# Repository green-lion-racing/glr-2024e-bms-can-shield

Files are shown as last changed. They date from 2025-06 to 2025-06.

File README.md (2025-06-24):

# CAN-Shield for NUCLEO-G474RE

NUCLEO-G474RE compatible CAN shield, which is our main microcontroller for the battery management system (BMS/AMS).

### Overview

Acts as can transciever for the BMS. 
Has two 12V output pins, one in case of a BMS fault. The other to set the state (on/off) of the HV charger.

CAN 1 is designated for the communication with FSGs datalogger, because of the high 1Mbit CAN baudrate.

CAN 2 is designated to communicate with the rest of the car, at a lower baudrate.

Compatible to the Analog Devices EVAL-ADBMS6822 board, can be directly slotted onto the nucleo board at the same time.

WR-TBL 3.5mm Connectors for signals to and from the board.

### Used parts

> [!WARNING]  
> Part list is not complete.

| Article | Description | Link | Quantity |
| --- | --- | --- | --- |
| Infineon TLE6250GV33XUMA1 | can transiever | https://www.mouser.de/ProductDetail/Infineon-Technologies/TLE6250GV33XUMA1?qs=OwbwYO03UsJ9UcCPEQ3lNA%3D%3D | 2 |
| Omron G5V-2-DC12 | relais | https://www.mouser.de/ProductDetail/Omron-Electronics/G5V-2-DC12?qs=lK7M36XCk6JxdWY%2FV6sVqw%3D%3D | 1 |
| STMicroelectronics ESDCAN01-2BLY | dual-line TVS diode | https://www.mouser.de/ProductDetail/STMicroelectronics/ESDCAN01-2BLY?qs=Ok1pvOkw6%2FpNzC2RQnWwPA%3D%3D | 2 |
| | transistor | | |
| Samsung CL10B104KB8NNNC | capacitor 100nF | https://www.mouser.de/ProductDetail/Samsung-Electro-Mechanics/CL10B104KB8NNNC?qs=349EhDEZ59rvGc2rLwVOdA%3D%3D | 2 |
| Vishay CRCW060368R1FKEA | resistor 68ohm | https://www.mouser.de/ProductDetail/Vishay-Dale/CRCW060368R1FKEA?qs=6z8JnUK2jyMngsBXu5il1A%3D%3D | 4 |
| Samtec SSW-119-01-T-D-LL | 02x19  Mounting Pin, 2.54 mm | https://www.mouser.de/ProductDetail/Samtec/SSW-119-01-T-D-LL?qs=F1JzWfReSMQC5N%252BZEM9ULw%3D%3D | 2 |
| Würth Elektronik 691321100002 | 2-pin header | https://www.mouser.de/ProductDetail/Wurth-Elektronik/691321100002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 | 1 |
| Würth Elektronik 691361100002 | 2-pin plug | https://www.mouser.de/ProductDetail/Wurth-Elektronik/691361100002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 | 1 |
| Würth Elektronik 691321100004 | 4-pin header | https://www.mouser.de/ProductDetail/Wurth-Elektronik/691321100004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 | 2 |
| Würth Elektronik 691361100004 | 4-pin plug | https://www.mouser.de/ProductDetail/Wurth-Elektronik/691361100004?qs=2kOmHSv6VfRmrzXJBP%2F4Sg%3D%3D | 2 |

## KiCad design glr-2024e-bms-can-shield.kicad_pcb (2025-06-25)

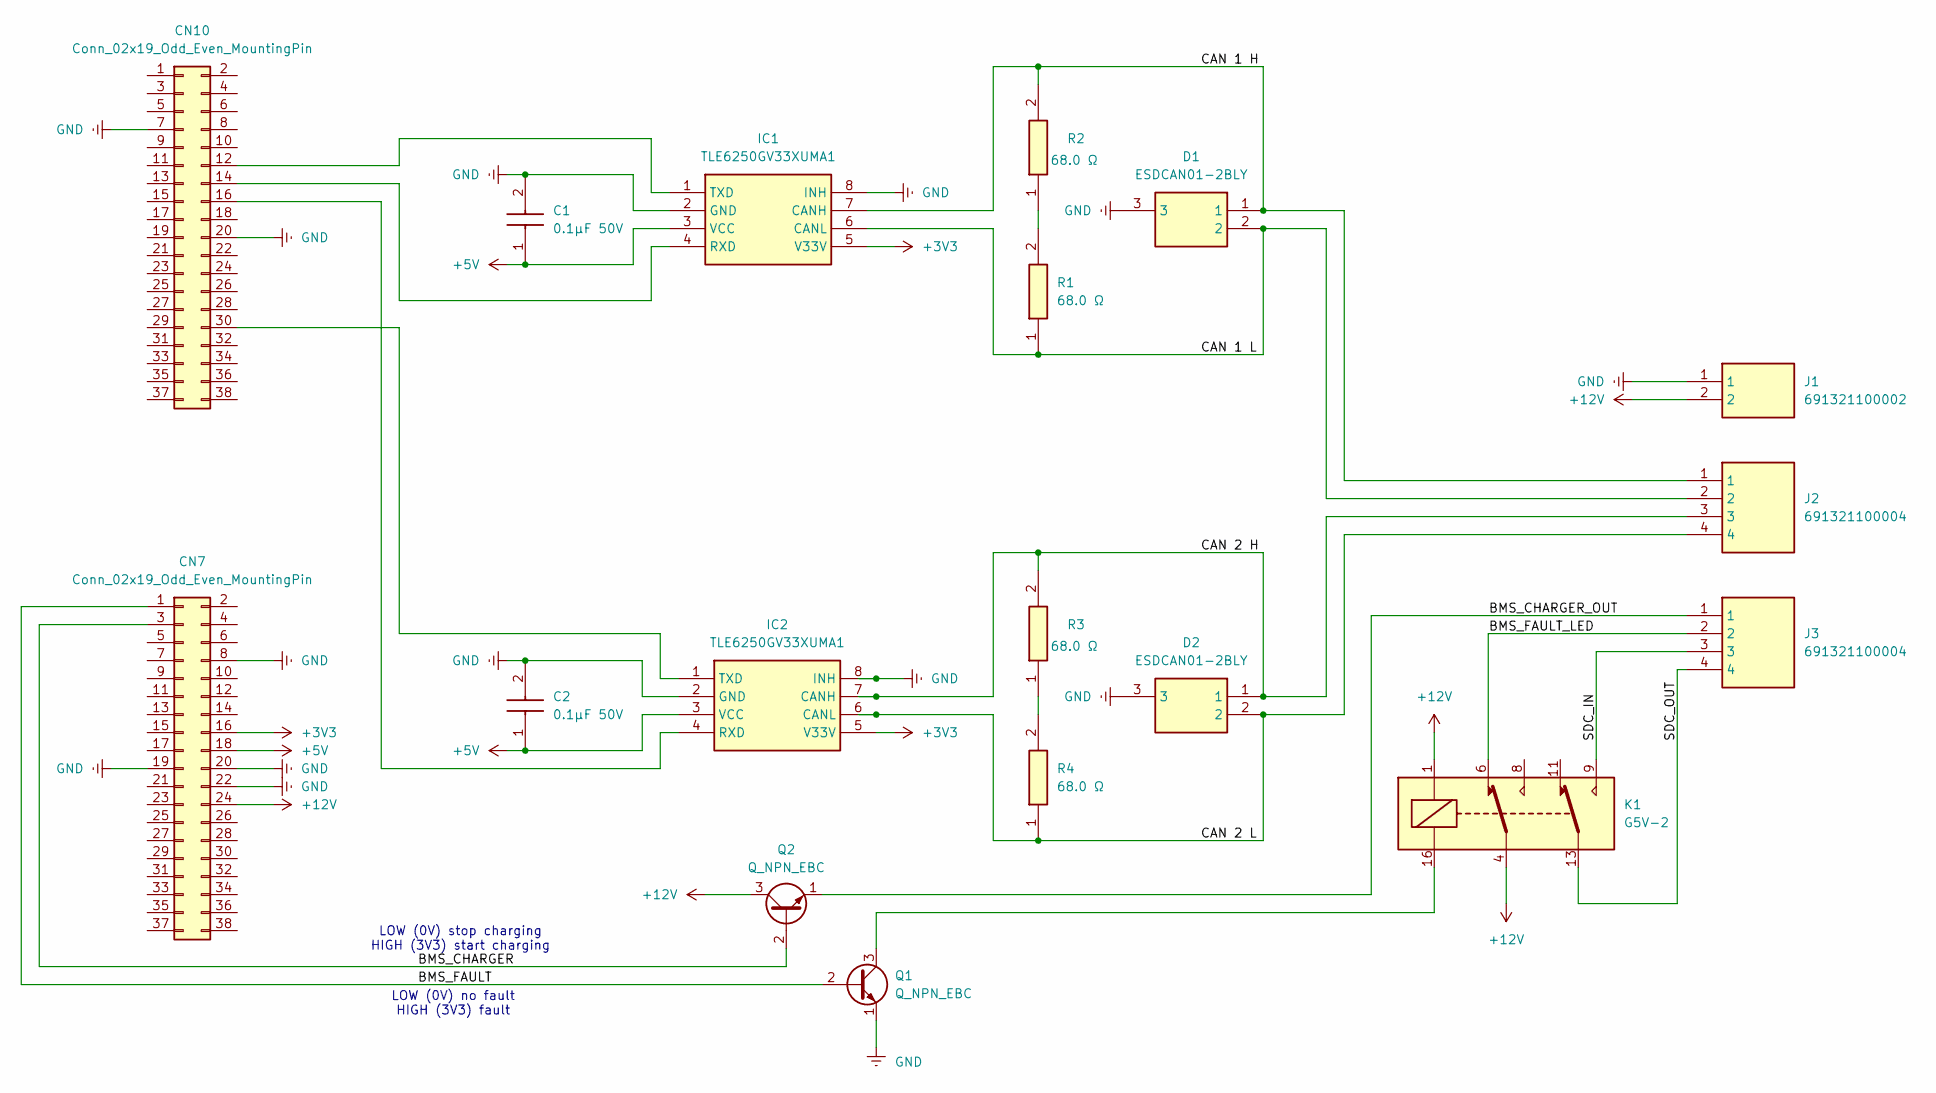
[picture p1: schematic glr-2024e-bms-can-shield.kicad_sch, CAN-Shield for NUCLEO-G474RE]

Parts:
C1, C2: 0.1μF 50V; CAPC1608X90N; Manufacturer_Part_Number CL10B104KB8NNNC
CN7, CN10: Conn_02x19_Odd_Even_MountingPin; PinSocket_2x19_P2.54mm_Vertical
D1, D2: ESDCAN01-2BLY; SOT95P255X125-3N; Mouser Part Number 511-ESDCAN01-2BLY
IC1, IC2: TLE6250GV33XUMA1; SOIC127P600X175-8N; Mouser Part Number 726-TLE6250GV33XUMA1
J1: 691321100002; Mouser Part Number 710-691321100002
J2, J3: 691321100004; Mouser Part Number 710-691321100004
K1: G5V-2; Relay_DPDT_Omron_G5V-2
Q1: Q_NPN_EBC; TO-18-3
Q2: Q_NPN_EBC; SOT-23
R1, R2, R3, R4: 68.0 Ω; RESC1608X50N; Manufacturer_Part_Number CRCW060368R1FKEA

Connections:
+3V3: CN7.16, IC1.5 (V33V), IC2.5 (V33V)
+5V: C1.1, C2.1, CN7.18, IC1.3 (VCC), IC2.3 (VCC)
+12V: CN7.24, J1.2, K1.1, K1.4, Q2.3 (C)
/BMS_CHARGER: CN7.3, Q2.2 (B)
/BMS_CHARGER_OUT: J3.1, Q2.1 (E)
/BMS_FAULT: CN7.1, Q1.2 (B)
/BMS_FAULT_LED: J3.2, K1.6
/CAN 1 H: D1.1, IC1.7 (CANH), J2.1, R2.2
/CAN 1 L: D1.2, IC1.6 (CANL), J2.2, R1.1
/CAN 2 H: D2.1, IC2.7 (CANH), J2.3, R3.2
/CAN 2 L: D2.2, IC2.6 (CANL), J2.4, R4.1
/SDC_IN: J3.3, K1.9
/SDC_OUT: J3.4, K1.13
GND: C1.2, C2.2, CN7.8, CN7.19, CN7.20, CN7.22, CN10.7, CN10.20, D1.3, D2.3, IC1.2 (GND), IC1.8 (INH), IC2.2 (GND), IC2.8 (INH), J1.1, Q1.1 (E)
unnamed: CN10.12, IC1.1 (TXD)
unnamed: CN10.14, IC1.4 (RXD)
unnamed: CN10.16, IC2.4 (RXD)
unnamed: CN10.30, IC2.1 (TXD)
unnamed: K1.16, Q1.3 (C)
unnamed: R1.2, R2.1
unnamed: R3.1, R4.2

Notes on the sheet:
LOW (0V) stop charging HIGH (3V3) start charging
LOW (0V) no fault HIGH (3V3) fault

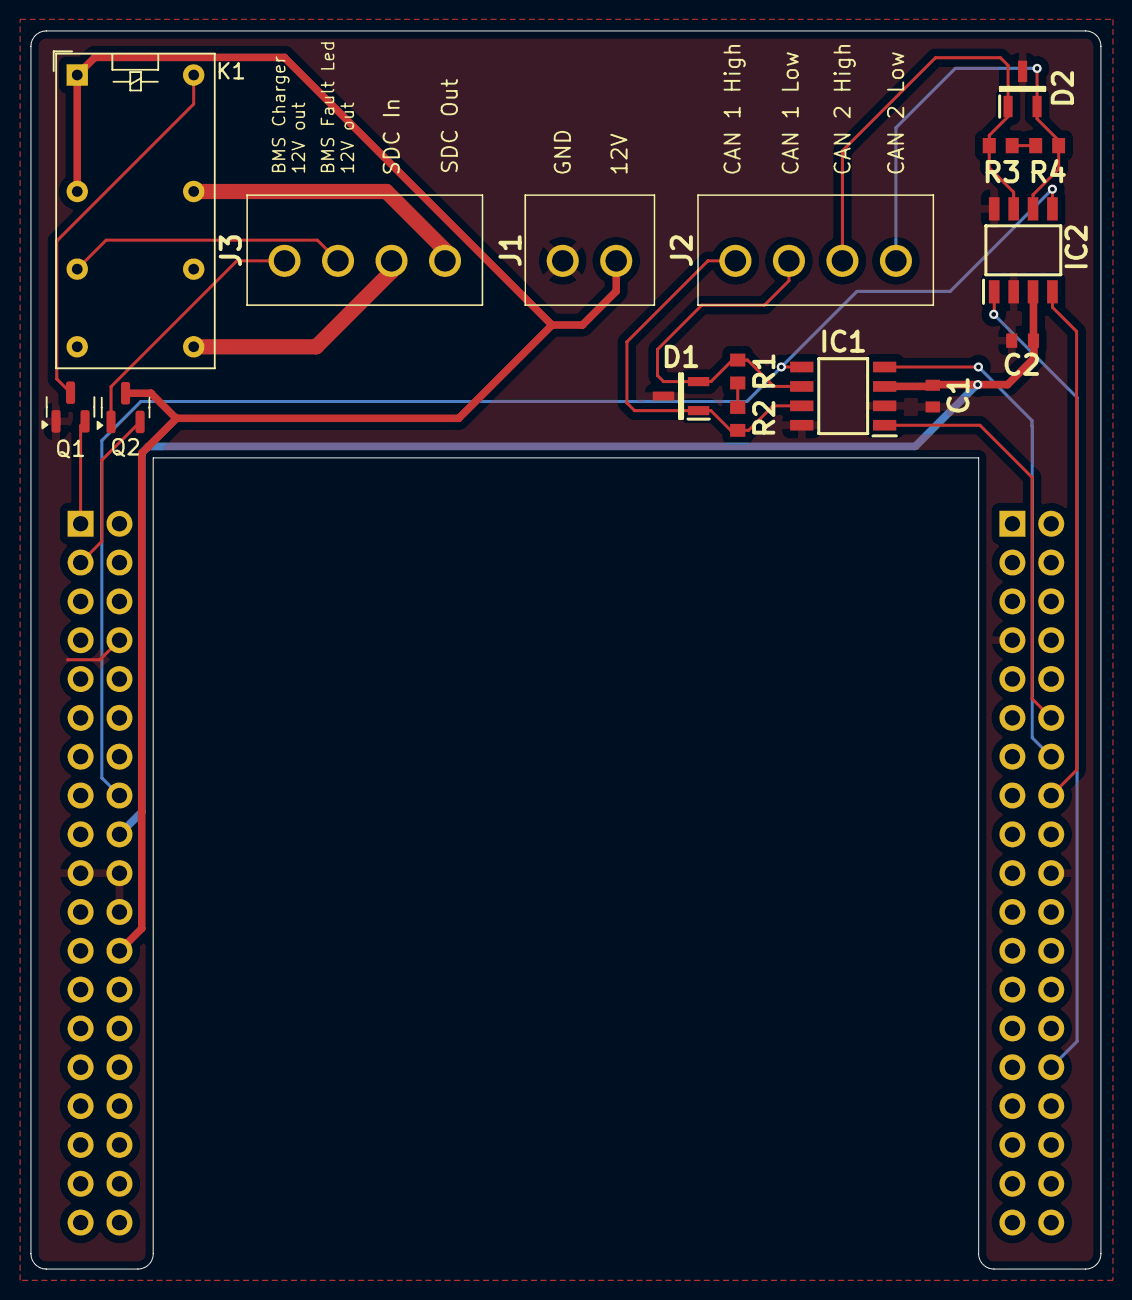
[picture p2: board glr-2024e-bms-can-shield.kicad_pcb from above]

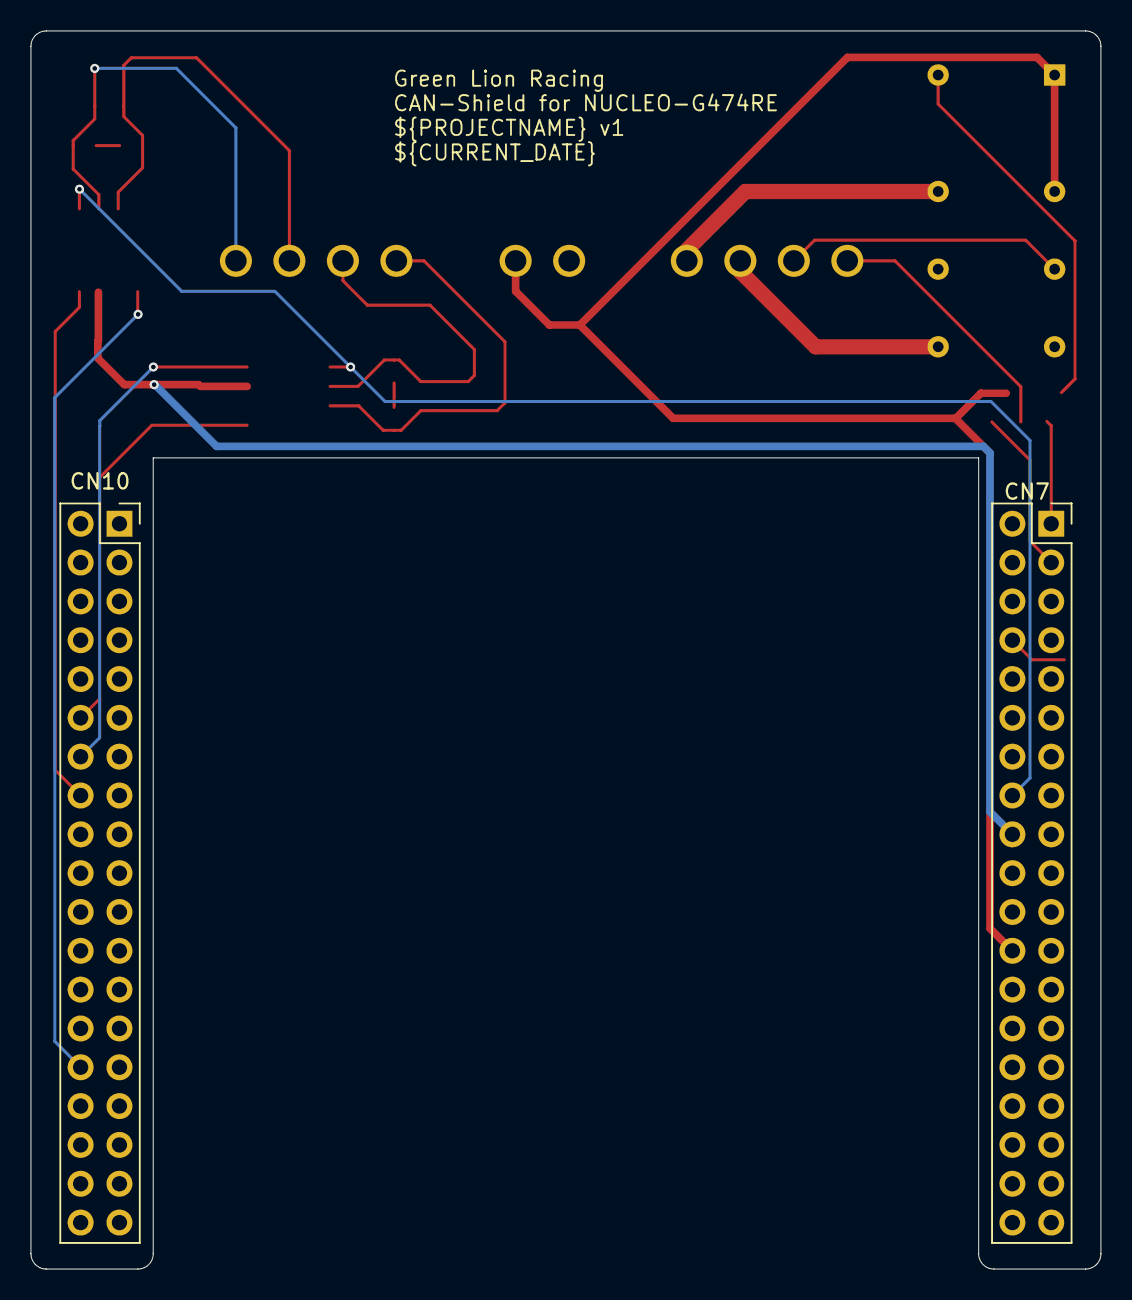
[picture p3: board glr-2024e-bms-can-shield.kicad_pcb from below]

Board: 2 copper layers, 70.0 x 81.0 mm, 18 parts (2 on the bottom side), 21 nets.

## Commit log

2025-06-07 Initial commit
    pcb should be done
    [glr-2024e-bms-can-shield.kicad_pcb, glr-2024e-bms-can-shield.kicad_sch]
2025-06-19 add relay and optocopler
    [glr-2024e-bms-can-shield.kicad_sch]
2025-06-21 the last touch
    I added two transistors. The first one replaces the optocoupler and controls the relay: when 3.3 V is present at the input (which indicates a fault), the transistor switches on and activates the relay. If no voltage is present, the relay remains off.
    The second transistor is used to turn the charger on and off. For this purpose, it was necessary to connect 12 V to its collector.
    [glr-2024e-bms-can-shield.kicad_pcb, glr-2024e-bms-can-shield.kicad_sch]
2025-06-21 more details to understand
    explaining how work the process between the socket and the transistors
    [glr-2024e-bms-can-shield.kicad_sch]
2025-06-22 use Würth Elektronik TBL connectors
    do some restructuring
    add project specific libraries
    [glr-2024e-bms-can-shield.kicad_pcb, glr-2024e-bms-can-shield.kicad_sch]
2025-06-23 set output path
    [glr-2024e-bms-can-shield.kicad_pcb]
2025-06-24 update needed parts
    not sure about these transistors
    add pdf to ignore list
    [glr-2024e-bms-can-shield.kicad_sch]
2025-06-24 forgor to save the file
    add plot output directory
    [glr-2024e-bms-can-shield.kicad_pcb]
2025-06-25 use current date as variable
    [glr-2024e-bms-can-shield.kicad_pcb, glr-2024e-bms-can-shield.kicad_sch]
